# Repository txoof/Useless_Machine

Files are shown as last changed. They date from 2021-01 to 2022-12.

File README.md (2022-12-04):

# Useless Machine

## *Absolutely Useless, Completely Necessary*

UM Demo

This useless machine comes with everything you need to laser cut and assemble a box and add hardware of your choice. Both designs physically disconnect the batteries when not in use to provide months and months of useless uselessness!

It even comes in two flavors:
## [ItsyBitsy Version](ItsyBitsy_Version/ItsyBitsy_README.md)

The ItsyBitsy version is sassy, slightly passive aggressive, has lights, is programmable and hackable! It runs on AdaFruit's Circuit Python and code is well documented and easily modified with options for adding additional attack/retreat modes.

There's even a PCB schematic you can spin out from OSH Park or one of the other fab houses.
## [555 Timer Version ](555_Version/555_README.md)

This version is a fun way to explore PWM and 555 timers. The venerable 555 is a great tool for making das blinken lights, but also for driving pulse-width-modulated hardware like servos.

The 555 Version requires just a few parts and can be fabricated at home with protoboard or etching your own circuit. There are resist masks, drill instructions, a BOM and everything you need to build a your own 555 Useless Machine.

## [The Box](./enclosure/Enclosure_README.md)

Fire up the pew-pew laser and make yourself a box! Everything you need to create your own laser-cut box is here including DXF, SVG, artwork and OpenSCAD files. The DXF and SVG versions are set up for 4mm birch ply. If you intend to use something thicker or thinner, make sure you generate a new layout using the OpenSCAD files.

The OpenSCAD version is customizable takes advantage of the OpenSCAD customizer interface. M

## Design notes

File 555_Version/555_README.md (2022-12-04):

# 555 Build Instructions

This version uses the venerable 555 timer to output a pulse-width modulated signal to drive a servo to max/min positions. This is a great way to learn more about the 555 and results in a cheap mechanism to drive an extremely simple useless machine.

I built this version to learn more about 555s and wrap my head around PWM signaling. I can't say that I'm an expert in either of these things now, but this project definitely helped me grow!

Check the [enclosure readme](../enclosure/Enclosure_README.md) for details on building a laser-cut enclosure.

## Circuit

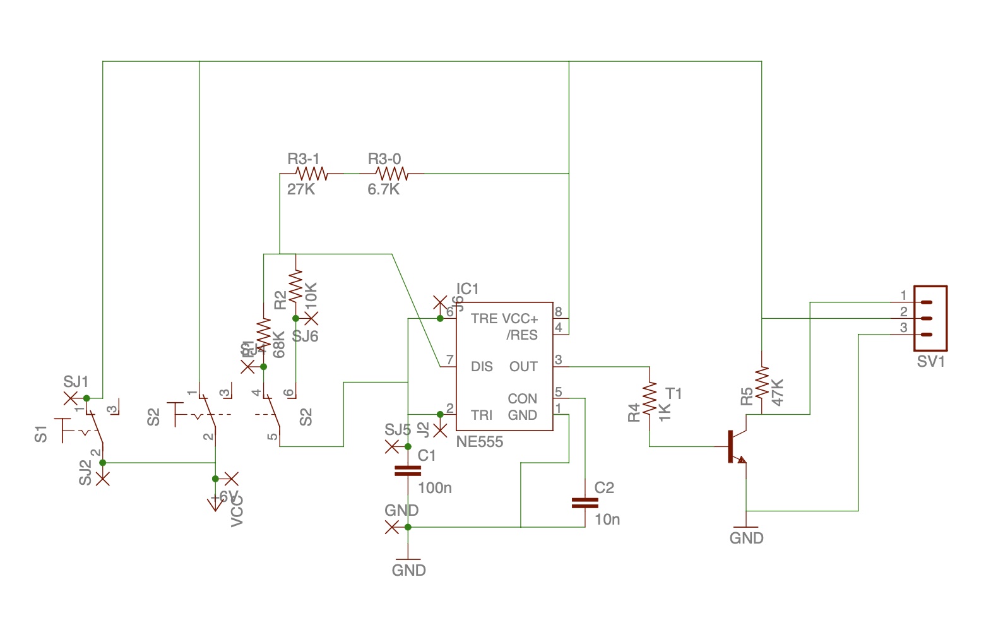
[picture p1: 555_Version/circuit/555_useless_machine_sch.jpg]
555 UM Schematic


### Bill of Materials

* S1 SPDT No/NC Roller Lever Micro Switch ([Omron SS-5GL2](https://nl.rs-online.com/web/p/micro-switches/6822660) or similar)
* S2 DPDT Panel Mount Toggle Switch ([RS PRO 734-7022](https://nl.rs-online.com/web/p/toggle-switches/7347022))
* IC1 [NE555P 8-Pin PDIP](https://nl.rs-online.com/web/p/timer-circuits/8660199)
* R1 68K
* R2 10K
* R3-1 27K
* R3-2 6.7K
* R4 1K
* R5 47K
* C1 100nF
* C2 10nF
* T1 2N2222
* [4x AA battery holder](https://nl.rs-online.com/web/p/battery-holders/1854643)
* 4x AA  battery
* 1501MG Servo or similar
* 1x3 2.54 mm Pin Headers
* hookup wire

## Circuit Board

You can build this up on prototype strip board, or use the included mask for etching your own using ferric chloride or hydrogen peroxide and muriatic acid method at home. It's pretty easy to do and some of the new toner transfer products make it pretty easy to do. Check this [instructables from TechShopJim](https://www.instructables.com/Sponge-Ferric-Chloride-Method-Etch-Circuit-Bo/) for more details.

The provided circuit board mask is for a single sided circuit and requires a couple of jumpers (see the layout). The mask is reversed and intended to go on the **bottom** of the etched board. 

* [Circuit Mask A4](./circuit/UM-Driver-rv3.1-A4.pdf)
* [Circuit Mask US Letter](./circuit/UM-Driver-rv3.1-Letter.pdf)
* [Circuit Layout w/ components](./circuit/UM-Board_Layout.pdf)

## Assembly

The Servo should run anti-clockwise when the microswitch is CLOSED and the toggle  switch is flipped toward the door.  The servo should run clockwise when the toggle switch is flipped away from the door.  

1. Etch board on a single sided copper clad pcb
2. Drill out holes:
    * Component holes are 1mm
    * Mounting holes and wire routing hole (near GND) are 3mm
3. Solder in components as shown in the board layout
4. Add a jumper wire betwen J2 and J6
5. SW1 Micro Switch is wired as Normally Open (NO)
6. SW2 DPDT switch is wired as follows:
    * SJ1 - pin 1 (same position as pin 4)  
    * SJ2 - common
    * SJ4 - pin 4 (same position as pin 1)  
    * SJ5 - common  
    * SJ6 - pin 6 
7. The signal wire of the servo is connected to pin 3 of the header; this is the pin closest to the 2N2222 transistor

## References

*hackster.io* [Controlling Servo Motor Using 555](https://www.hackster.io/techmirtz/controlling-servo-motor-using-555-dd3a33)

*EngineersGarage*: [Servo Motor Control Using a 555 Timer IC](https://www.engineersgarage.com/servo-motor-control-using-555-timer-ic/)

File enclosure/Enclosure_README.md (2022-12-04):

# Laser Cut Enclosure

Everything you need to build a laser cut enclosure is right here. The DFX and SVG versions are set up for a material thickness of ~4mm. There's even some nice artwork you can add to the outside. These instructions assume you have a working circuit and are ready to mount it in the box.

If you'd like to do some more customization or intend to use material that is not 4mm in thickness, the OpenSCAD files are designed to be hacked and modified. Check the [OpenSCAD Customization](#openscad-customization) section below for some guidance.

The lovely artwork on the outside of the box is courtesy of Patricia M. Ciuffo.

Useless Machine

## OpenSCAD Customization

If you intend to use material that is not ~4mm in thickness, you **must** adjust the material thickness variable. You can easily access this by grabbing the [OpenSCAD](./OpenSCAD/) files and libraries. Open [`useless_machine.scad`](./OpenSCAD/useless_machine.scad) and use the *Customizer* to change the `thick` (Material Thickness) value in the *Project Setup* section.

Adjusting the thickness will recalculate the finger cuts along the edges and adjust some of the other design values. Major adjustments to the thickness may impact other values. Make sure you check the 3D model for interferences and other issues.

To generate a new DXF or SVG file switch to the 2D view (*Customizer > Project Setup > 2D*). You will need to render the project (F6 or *Design > Render*) and then export the DXF or SVG (*File > Export > SVG|DXF*).

*NOTES:*

* The 3D view deliberately leaves off several of the faces. This is just to make viewing easier. They are indeed accounted for in the 2D production.
* It is possible to 3D print this enclosure, but the finger joints will likely not fit together. You will need to do some sanding of your finished parts, or change up the algorithm that calculates the inside/outside dimensions.

## Case Files

| File | Notes |
|---|---|
| [useless_machine.dxf](./useless_machine-1.34.dxf) | Case outline only compatible with lasercutting software (material thickness ~4mm) |
| [useless_machine.svg](useless_machine-1.34.svg) | Case outline as a scallable vector graphic. Use this version if you'd like to add your own vector/raster artwork (material thickness ~4mm) |
| [useless_machine.zip](./useless_machine-SCAD.zip) | Customizable OpenSCAD code for generating SVG or DXF output. Use this version if you'd like to customize the dimensions or material thickess. |
| [useless_machine_artwork.zip](./usless_machine_artwork) | Adobe Illustrator vector graphics that can be used to decorate the outside of the enclosure. |
| [OpenSCAD Files](./OpenSCAD/)| All the required files for customizing your design and generating new DXF and SVG Files|

## Assembly

| | | |
|-|-|-|
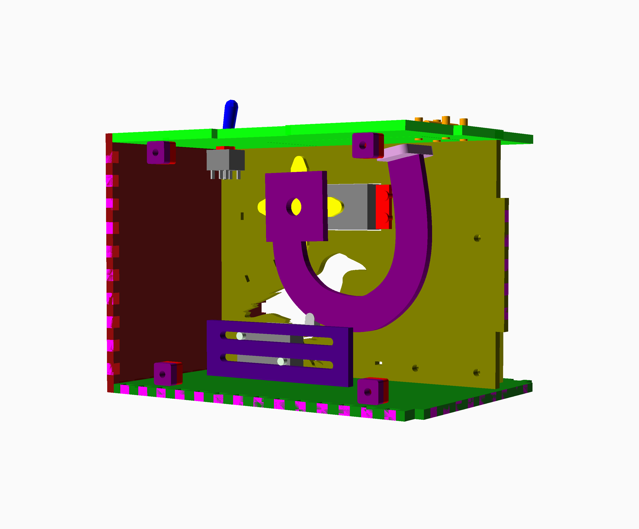
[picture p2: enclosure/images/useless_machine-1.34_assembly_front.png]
assembly front
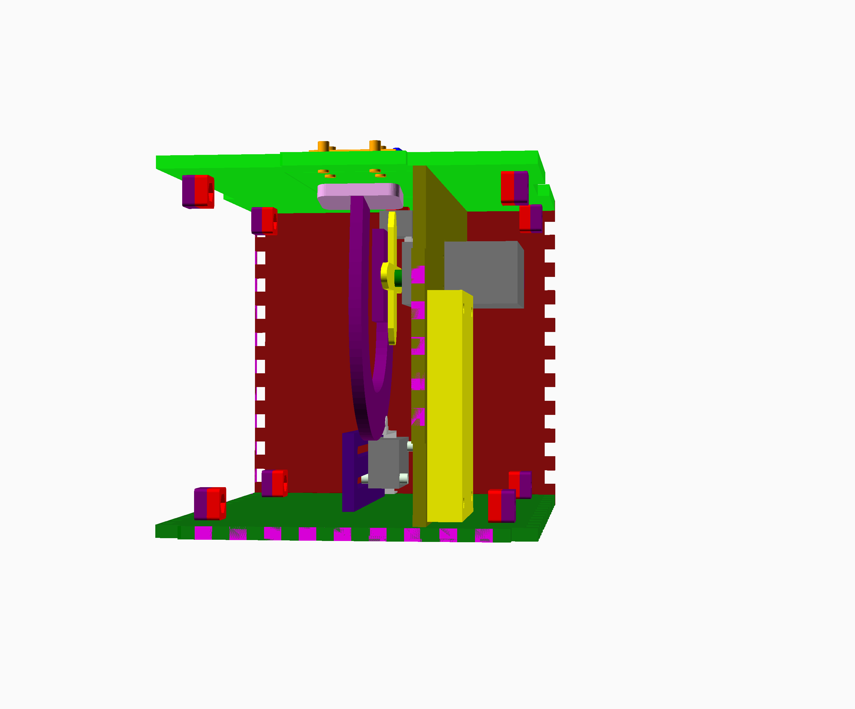
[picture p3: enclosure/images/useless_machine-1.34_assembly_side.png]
assembly side
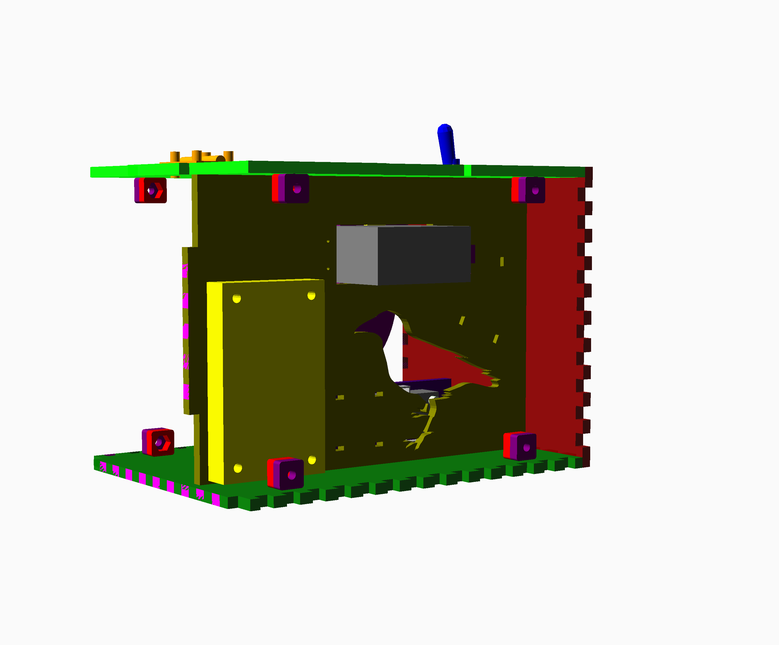
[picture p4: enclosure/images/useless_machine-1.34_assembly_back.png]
assembly back
| <br/> FRONT| | <br/> BACK|

### Materials

* 10x M3 Bolts
* 8x M3 Nuts
* 2x M2 or M3 Bolts and matching nuts
* Small hinge and bolts or screws 16mm between holes and 13mm from across faces
* PLA (wood) Glue
* Appropriate servos, switches, batteries, etc.

## Construction

The laser-cut faces should fit together logically. Use the illustrations and annotated image below to help identify the parts and orientations. 

Lay the bottom face in front of you so that the microswitch support is closest to you and oriented to the left side of the bottom plate. Slot the internal support into the bottom face. The crow should be facing to your right and should be directly in front of the microswitch support. Check the images above for reference.

Slot the microswitch support into the bottom plate. The support should be located in front of the bird cut-out.

Slot in the left and right sides. These are interchangeable unless you've decorated them.

Check the fit of the front, back and lid and then set the front, back and lid aside. Use a small amount of PLA glue to attach the supports and sides. DO NOT GLUE THE FRONT, BACK OR LID!

### Install PCB and Battery

If you are using the either of the supplied PCBs from this project, the holes should line up with the PCB Mount holes on the inside support. Use either wooden spacers or washers to raise the PCB a bit and then use M3 bolts and nuts to secure.

Depending on the mounting options for your battery pack, you can either use velcro, hot-glue or drill holes to mount it. 

Route any wires for the microswitch or DPDT switch through the bird cutout.

### Catch Construction

Build 4x LID catches using one fastener with a bolt hole, one tabbed fastener and an M3 bolt. Glue the two fastener pieces together, then glue the M3 nut into hexagonal hole. It helps to put a bolt through the nut to prevent the threads from filling with glue.
| | |
|-|-|
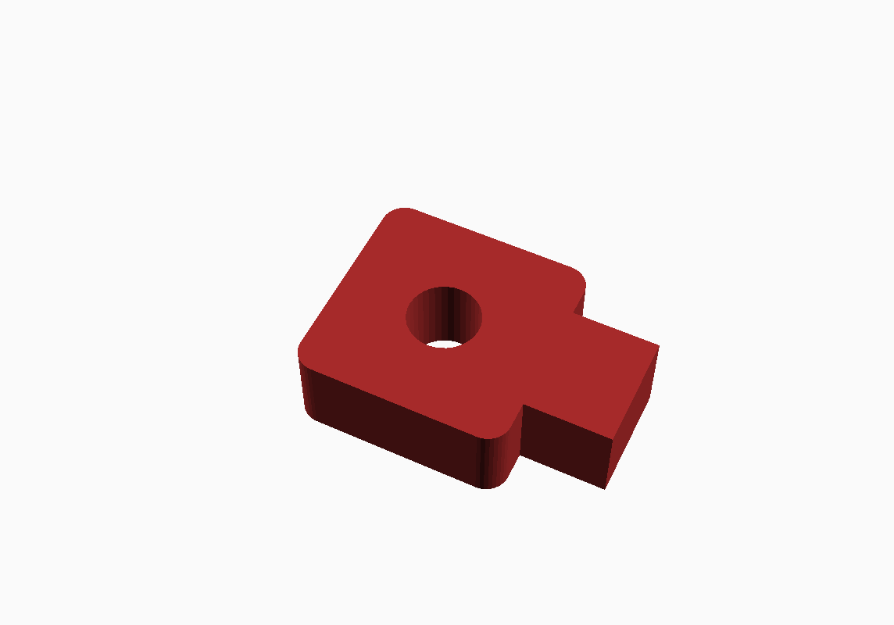
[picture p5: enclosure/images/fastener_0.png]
bolt hole fastener
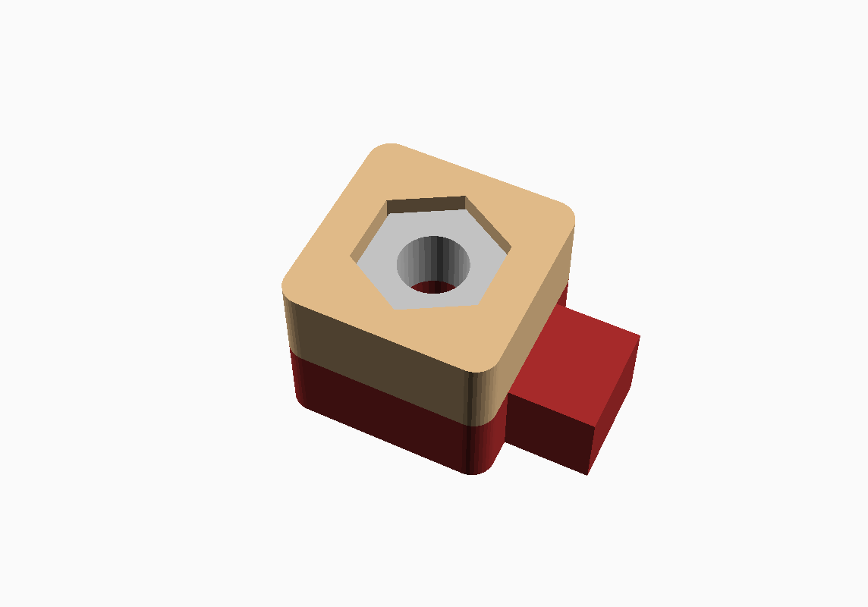
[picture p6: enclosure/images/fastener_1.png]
tabbed fastner
|| |

Build 3x BOTTOM catches using one fastener with a bolt hole, two tabbed fastener and an M3 bolt. Glue the two fastener pieces together, add an M3 nut into hexagonal hole then glue on the last tabbed fastener, but with the tab facing the opposite direction. These will be used in the fastener locations in the bottom face. Wait to glue these in until 

| | | |
|-|-|-|
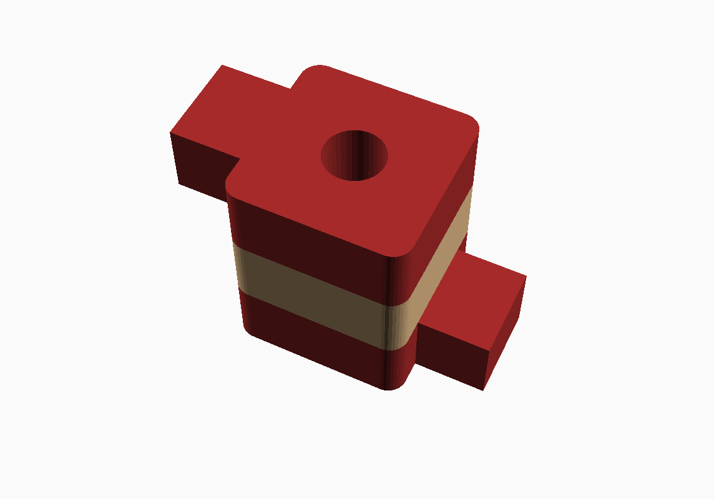
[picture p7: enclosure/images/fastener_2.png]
full stack
|bolt hole fastener|tabbed fastner ||

### Attach the Catches

UM Catches

Glue the catches into place on the lid using the method below. This method helps ensure that the catches are properly aligned with the bolt holes and the front and back faces will sit snugly.

1. Thread an M3 Bolt through the top two holes of the front and back faces
2. Loosely screw one LID catch onto the bolt so the nut is facing inwards
3. Starting with the front face, put a small dab of glue onto the two lid catches
4. Fit the face onto the base and seat all the fingers on the left and right sides
5. Orient the tabs on the LID catches so they are facing upwards
6. Place the lid on the box seating the glue-covered tabs into the fastener locations
7. Tighten the bolts so they are **finger** tight and ensure the tabs are fully seated in the lid
8. Allow the glue to dry
9. Repeat for the back face

Glue three BOTTOM catches into place on the base using the same method as the lid. Start with one side, then do the other. Depending on the thickness of your PCB, you will need to find the best possible solution for the catch directly in front of it.

### Install the Lid and Door Jamb

Using either small wood screws, or small bolts, attach the hinge to the top and the door in the lid. I added a bit of silver plastic from an anti-static bag using double stick tape to the back of the door to decrease the friction with the arm as it pushed open the door. This is optional.

If your lid does not close on its own, adding a small spring between the bolts of the hinge can help it snap back shut. A small spring out salvaged from a clicky ball-point pen worked great for this. This is optional.

To keep the lid from flopping too far inside the box, you will need to glue the door jamb to the underside of the lid. The jamb should be glued so the lip of the door opposite the hinge just rests on it.

UM door jamb

### Install the Switches

Use the raven shaped hole in the internal wall to route your wires from the PCB side of the box to the larger space opposite the PCB. 

The DPDT switch is installed in the lid through the provided hole using the nuts supplied with the switch. If your switch rotates too much, consider adding some small pieces of wood on either side (see image above).

The SPDT micro switch is installed on the Microswitch Support using two bolts and nuts. Attach the switch on the inside of the support closest to the internal wall. Loosely attach the switch for now. It will need to be adjusted after the arm is installed.

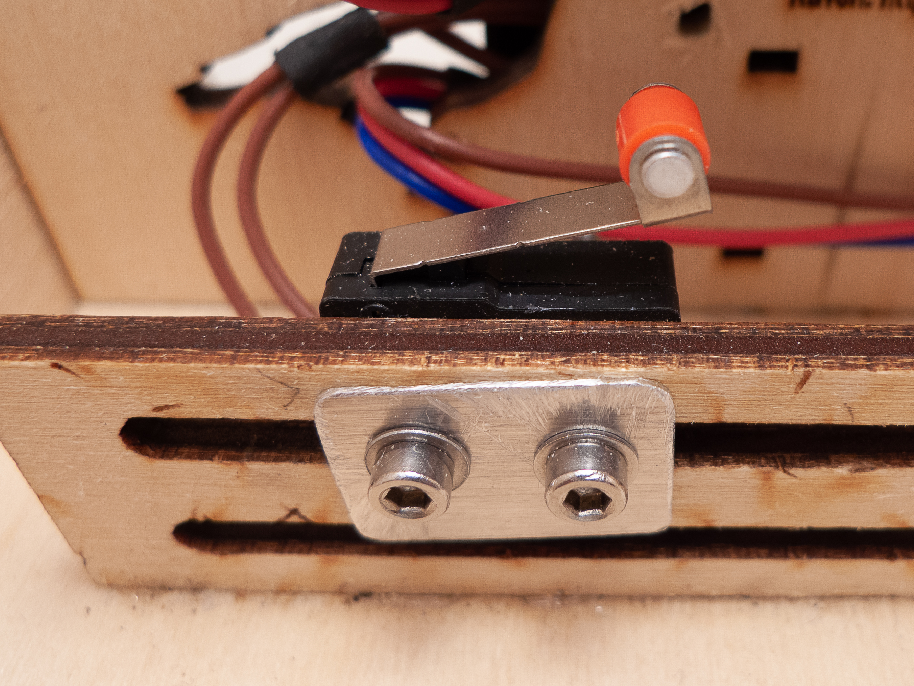
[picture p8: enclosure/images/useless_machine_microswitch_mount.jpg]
UM microswitch mount


### Install the Servo and Arm

Attach the arm to the servo horn (black or white plastic disk) supplied with the servo. Use small wood screws.  Glue the pusher face onto the arm using PLA glue.

Working from the side opposite the PCB, mount the servo so the horn (drive side) is on the same side as the microswitch. Screw the servo in place using the small wood screws supplied with the servo.

Rotate the servo clockwise until it stops. Turn it back anti-clockwise slightly less than 1/4 turn. Attach the arm and horn assembly to the servo using the screw supplied with the servo so that the arm is all the way retracted and just about touching the microswitch (see the image).

Manually rotate the arm and make sure that the pusher head can make it all the way to the switch and go just a bit further. If the arm cannot reach the switch, unmount the arm and turn the servo clockwise a few degrees. Attach the arm and try again. Repeat as needed.

UM Servo and Arm

### Adjust the Microswitch

For both the 555 and ItsyBitsy designs provided, when the arm touches the microswitch, it signals that the arm has returned *home*. For the 555 version, this disconnects the battery entirely. The ItsyBitsy version starts a countdown timer and after a preset time, disconnects a latching relay to disconnect the battery.

For both designs, the position of the limit switch is important. Limit switches come in a lot of variety with long levers, rollers and require a variety of force to switch. Slide the microswitch on the support left and right until you can find a position where the arm is completely inside the box **and** the switch is activated. 

As long as the arm isn't bottoming out and crashing into the bottom of the box, or hitting the limit of the servo, any position where the arm is entirely inside the box will work. Play with it until you find a solution you like.

### Close It Up

Tie up all your loose wires using zip ties or some twist-ties. Use the M3 bolts to close up the box and enjoy!

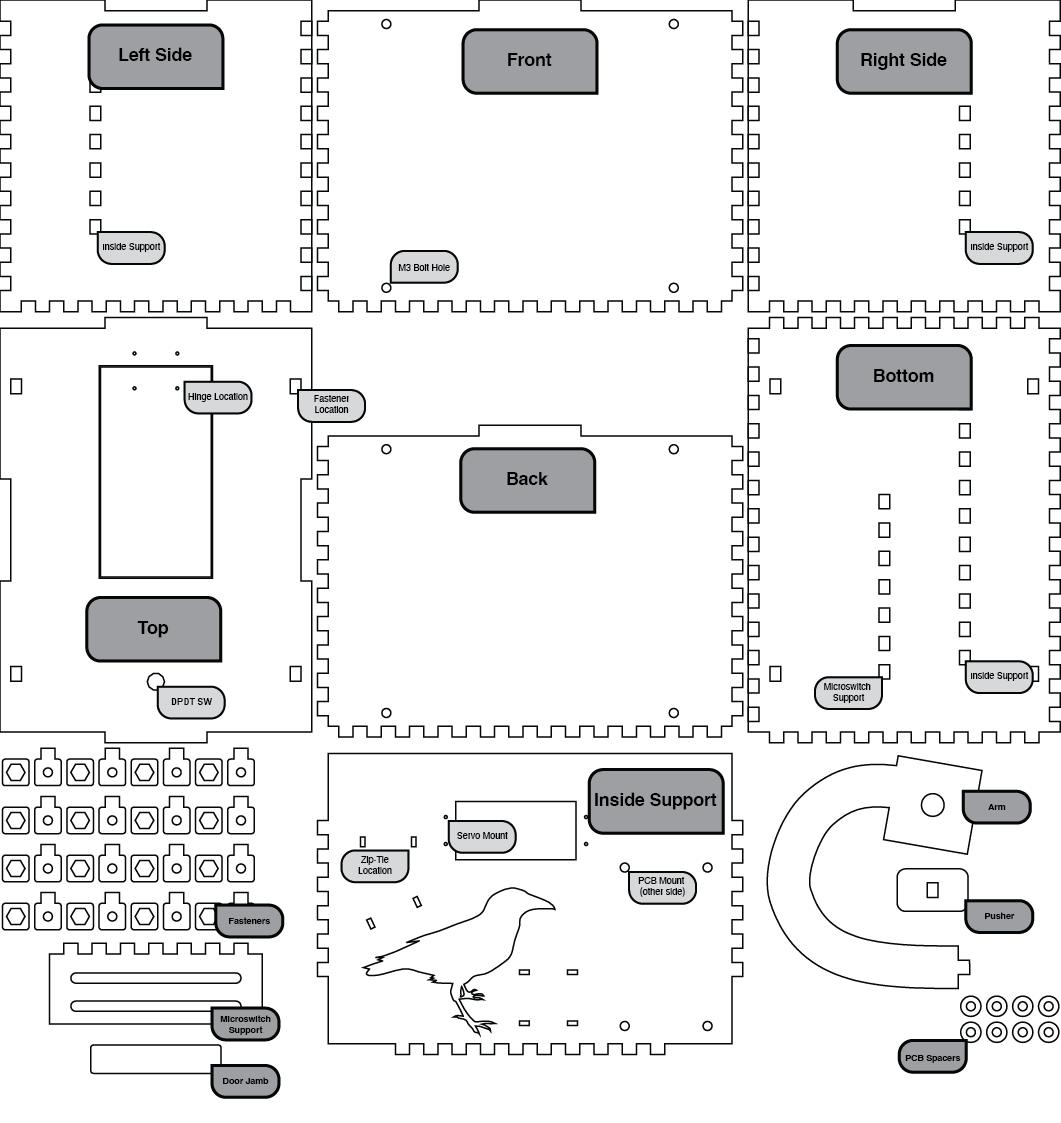
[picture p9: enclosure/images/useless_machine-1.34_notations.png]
annotated layout


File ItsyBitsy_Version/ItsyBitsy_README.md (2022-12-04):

# ItsyBitsy Useless Machine

This useless machine runs off of an AdaFruit 5V ItsyBitsy running CircuitPython. It's got sassy, random responses, neo-pixle bling and it's just as useless and **AWESOME** as all the rest.

To get the 

This design runs off of 4xAA batteries and uses a latching relay and some clever double pull double throw magic to completely disconnect the battery when it's not in use so it won't chooch through your AAs like crazy.

If you want to have your own PCB milled, you can also find the Eagle design files. I have a few extra PCBs sitting around for anyone that's interested. I'll ship them to the first lucky people that ask.

Useless Machine!

## Code

Find the code and necessary libraries in the [CircuitPython](./CircuitPython/) directory

### Pinouts

```python
# bottom limit switch (micros switch)
LIMIT_SWITCH_PHY = board.D9
# top direction switch (dpdt)
DIRECTION_SWITCH_PHY = board.D7
# servo PWM
SERVO_PWM_PHY = board.D10
# send +3v pulse to switch off relay
RELAY_OFF_PHY = board.D13
# NeoPixel driver PIN
PIXEL_PWM_PHY = board.A1
```
## Bill of Materials

[Eagle CSV version](./circuit/UM%20V2%20ItsyBitsy.csv)

|Part |Value|Device |Package |Description|ALLIED_NUMBER|DESCRIPTION |HEIGHT|MANUFACTURER_NAME|MANUFACTURER_PART_NUMBER|
|-|-|-|-|-|-|-|-|-|-|
|LED1 |LTST-C930KRKT|LTST-C930KRKT|LTSTC930KRKT|LED, Red LTST-C930KRKT, Lite-On 631 nm 3125 (1210) SMD package | |LED, Red LTST-C930KRKT, Lite-On 631 nm 3125 (1210) SMD package|2.5mm |Lite-On|LTST-C930KRKT |
|K1 |DS2E-SL2-DC5V|DS2E-SL2-DC5V|DS2ESL2DC5V |Low Signal Relays - PCB 2A 5VDC DPDT LATCHING PCB|70158678 |Low Signal Relays - PCB 2A 5VDC DPDT LATCHING PCB |10.2mm|Panasonic|DS2E-SL2-DC5V |
|C1 |470|CPOL-USE2,5-6E |E2,5-6E |POLARIZED CAPACITOR, American symbol | ||| ||
|D1 |1N4004 |1N4004 |DO41-10 |DIODE| ||| ||
|DIRECTIONSW|Direction Sw |CONN_04POLAR |MOLEX-1X4 |Multi connection point. Often used as Generic Header-pin footprint for 0.1 inch spaced/style header connections| ||| ||
|EXTPOWER |Limit Sw |CONN_02POLAR |MOLEX-1X2 |Multi connection point. Often used as Generic Header-pin footprint for 0.1 inch spaced/style header connections| ||| ||
|LIMITSW|Limit Sw |CONN_02POLAR |MOLEX-1X2 |Multi connection point. Often used as Generic Header-pin footprint for 0.1 inch spaced/style header connections| ||| ||
|NEOPIXEL |7x |CONN_03POLAR |MOLEX-1X3 |Multi connection point. Often used as Generic Header-pin footprint for 0.1 inch spaced/style header connections| ||| ||
|Q1 |2N3904 |MPS2222A-NPN-TO92-CBE|TO92-CBE|NPN Transistror| ||| ||
|R1 |100|R-US_M1206 |M1206 |RESISTOR, American symbol| ||| ||
|R2 |220|R-US_M1206 |M1206 |RESISTOR, American symbol| ||| ||
|SERVO|1051 M |CONN_03POLAR |MOLEX-1X3 |Multi connection point. Often used as Generic Header-pin footprint for 0.1 inch spaced/style header connections| ||| ||
|U$1|ITSYBITSY3V|ITSYBITSY3V|ITSYBITSY3V |AdaFruit ItsyBitsy M4 3V | ||| ||

## Eagle Files

Find the eagle files in the [circuit](./circuit/) folder.

I've had lots of success working with [OSH Park](https://oshpark.com/). Their instructions are incredibly clear and the service is great.

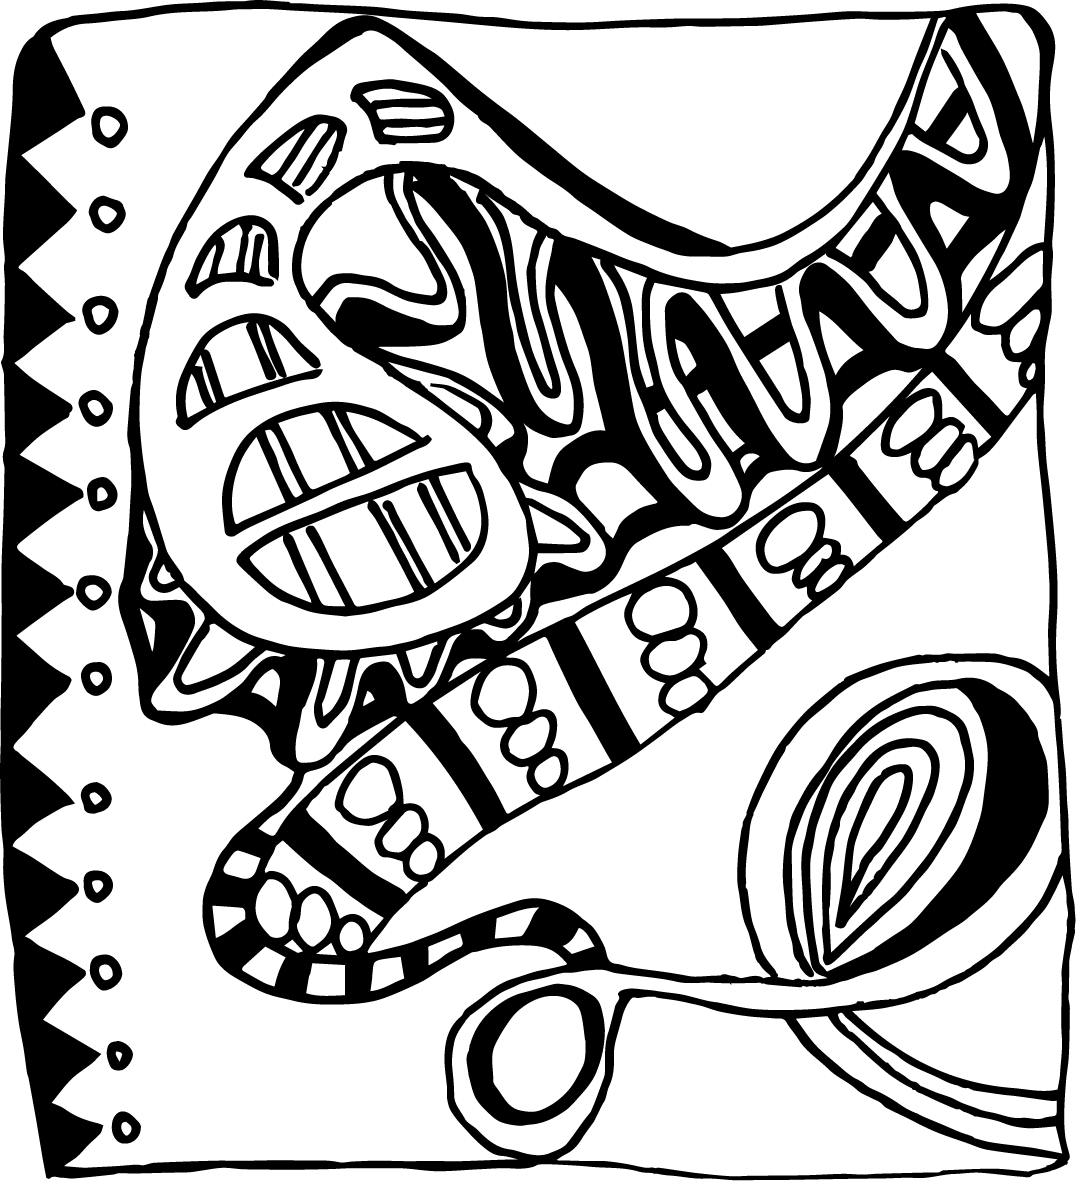
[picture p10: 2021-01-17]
enclosure/usless_machine_artwork/FaceA_Arches.tif

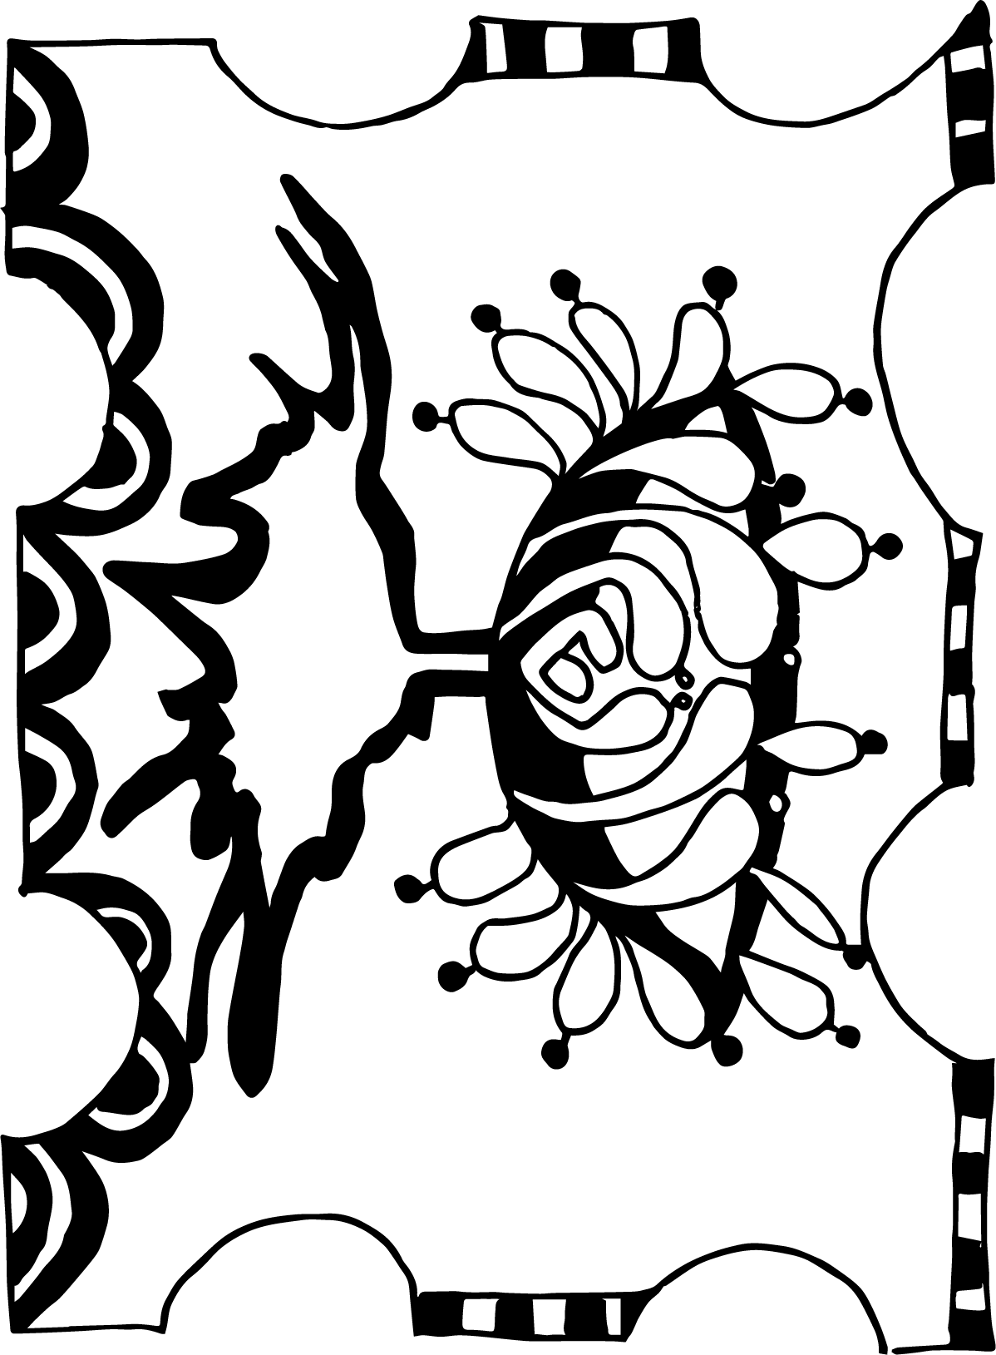
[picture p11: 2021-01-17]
enclosure/usless_machine_artwork/FaceBC_Cup.tif

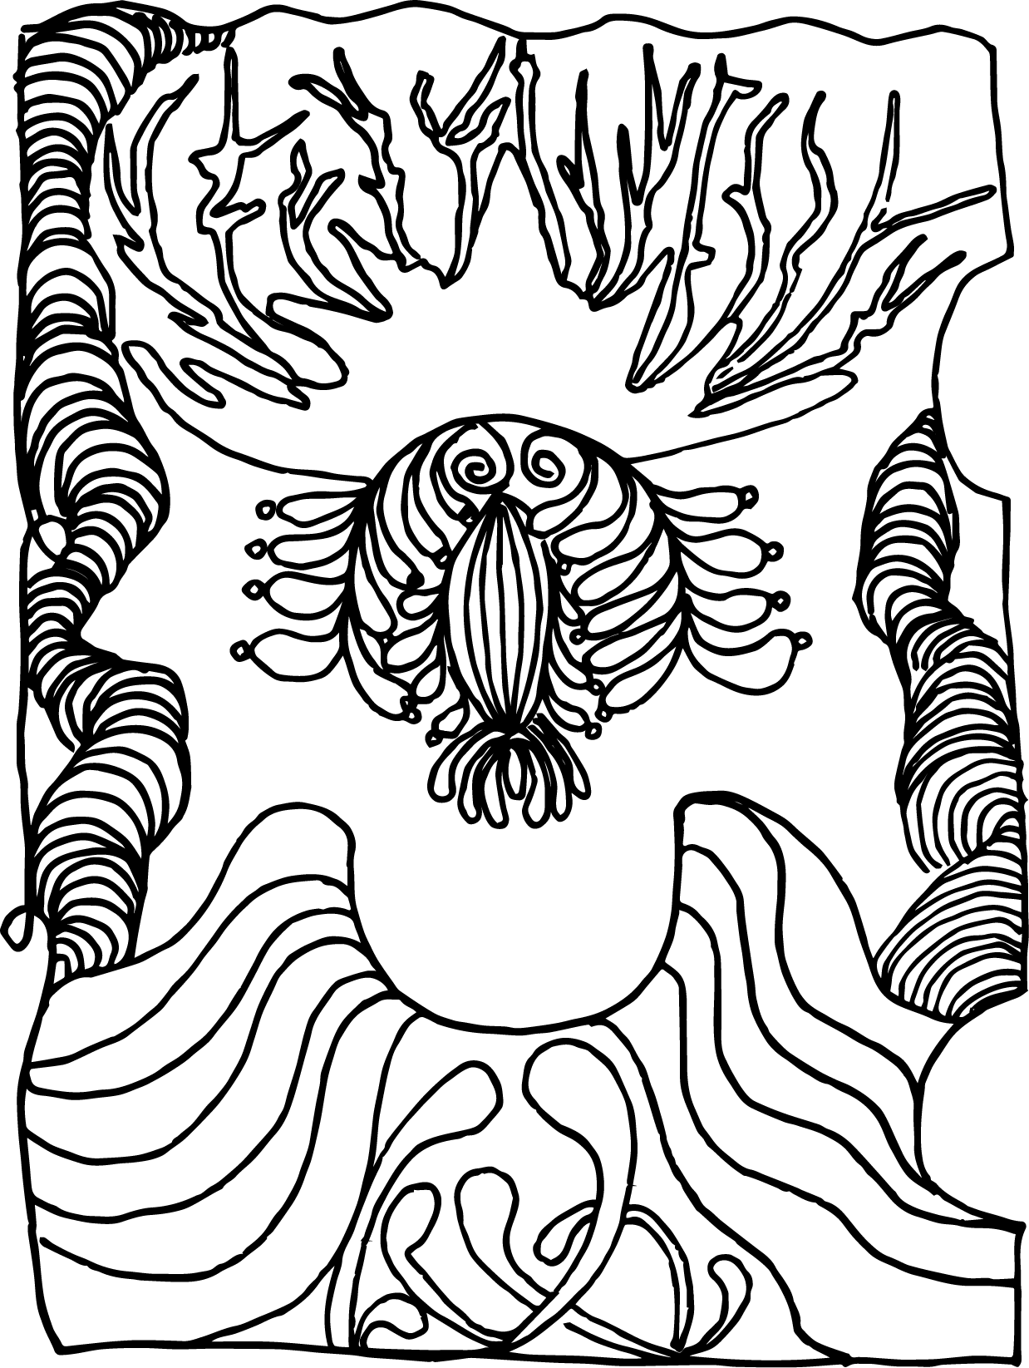
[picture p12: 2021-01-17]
enclosure/usless_machine_artwork/FaceBC_Flower Vertical_lid.tif

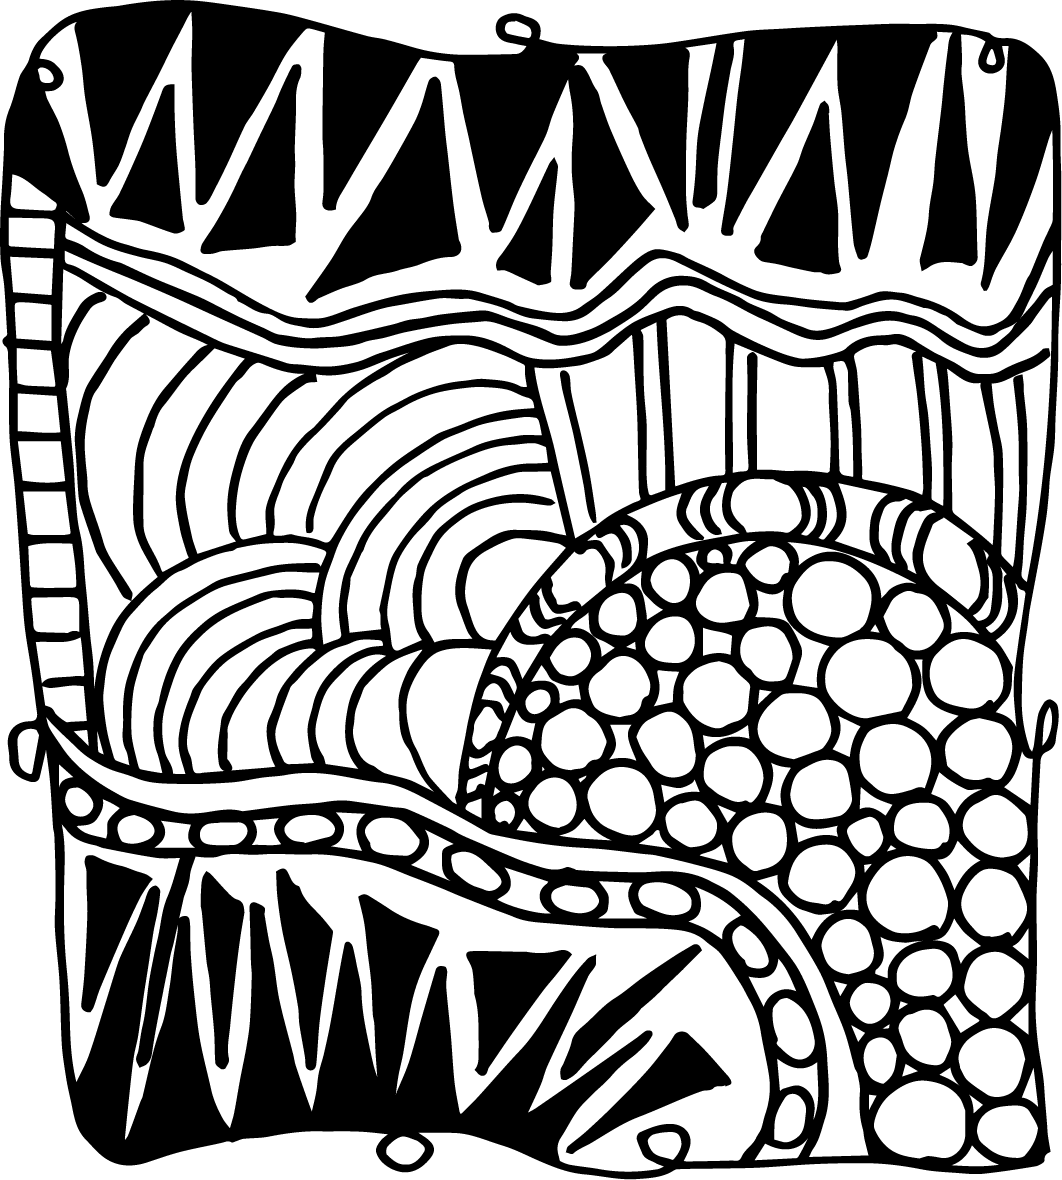
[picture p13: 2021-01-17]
enclosure/usless_machine_artwork/FaceA_Bubbles.tif

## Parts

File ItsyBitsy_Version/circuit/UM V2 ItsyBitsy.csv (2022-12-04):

Part | Value | Device | Package | Description | ALLIED_NUMBER | DESCRIPTION | HEIGHT | MANUFACTURER_NAME | MANUFACTURER_PART_NUMBER | MOUSER_PART_NUMBER | MOUSER_PRICE-STOCK | POPULARITY | PROD_ID | RS_PART_NUMBER | RS_PRICE-STOCK | SF_ID | SPICEPREFIX
C1 | 470 | CPOL-USE2,5-6E | E2,5-6E | POLARIZED CAPACITOR, American symbol |  |  |  |  |  |  |  |  |  |  |  |  | C
D1 | 1N4004 | 1N4004 | DO41-10 | DIODE |  |  |  |  |  |  |  | 82
DIRECTIONSW | Direction Sw | CONN_04POLAR | MOLEX-1X4 | Multi connection point. Often used as Generic Header-pin footprint for 0.1 inch spaced/style header connections |  |  |  |  |  |  |  |  | CONN-08186 |  |  | PRT-08231
EXTPOWER | Limit Sw | CONN_02POLAR | MOLEX-1X2 | Multi connection point. Often used as Generic Header-pin footprint for 0.1 inch spaced/style header connections |  |  |  |  |  |  |  |  |  |  |  | PRT-09918
K1 | DS2E-SL2-DC5V | DS2E-SL2-DC5V | DS2ESL2DC5V | Low Signal Relays - PCB 2A 5VDC DPDT LATCHING PCB | 70158678 | Low Signal Relays - PCB 2A 5VDC DPDT LATCHING PCB | 10.2mm | Panasonic | DS2E-SL2-DC5V
LED1 | LTST-C930KRKT | LTST-C930KRKT | LTSTC930KRKT | LED, Red LTST-C930KRKT, Lite-On 631 nm 3125 (1210) SMD package |  | LED, Red LTST-C930KRKT, Lite-On 631 nm 3125 (1210) SMD package | 2.5mm | Lite-On | LTST-C930KRKT | 859-LTST-C930KRKT | https://www.mouser.com/Search/Refine.aspx?Keyword=859-LTST-C930KRKT |  |  | 1689768 | http://uk.rs-online.com/web/p/products/1689768
LIMITSW | Limit Sw | CONN_02POLAR | MOLEX-1X2 | Multi connection point. Often used as Generic Header-pin footprint for 0.1 inch spaced/style header connections |  |  |  |  |  |  |  |  |  |  |  | PRT-09918
NEOPIXEL | 7x | CONN_03POLAR | MOLEX-1X3 | Multi connection point. Often used as Generic Header-pin footprint for 0.1 inch spaced/style header connections |  |  |  |  |  |  |  |  | CONN-08625 |  |  | PRT-08096
Q1 | 2N3904 | MPS2222A-NPN-TO92-CBE | TO92-CBE | NPN Transistror |  |  |  |  |  |  |  | 0
R1 | 100 | R-US_M1206 | M1206 | RESISTOR, American symbol |  |  |  |  |  |  |  |  |  |  |  |  | R
R2 | 220 | R-US_M1206 | M1206 | RESISTOR, American symbol |  |  |  |  |  |  |  |  |  |  |  |  | R
SERVO | 1051 M | CONN_03POLAR | MOLEX-1X3 | Multi connection point. Often used as Generic Header-pin footprint for 0.1 inch spaced/style header connections |  |  |  |  |  |  |  |  | CONN-08625 |  |  | PRT-08096
U$1 | ITSYBITSY3V | ITSYBITSY3V | ITSYBITSY3V | AdaFruit ItsyBitsy M4 3V

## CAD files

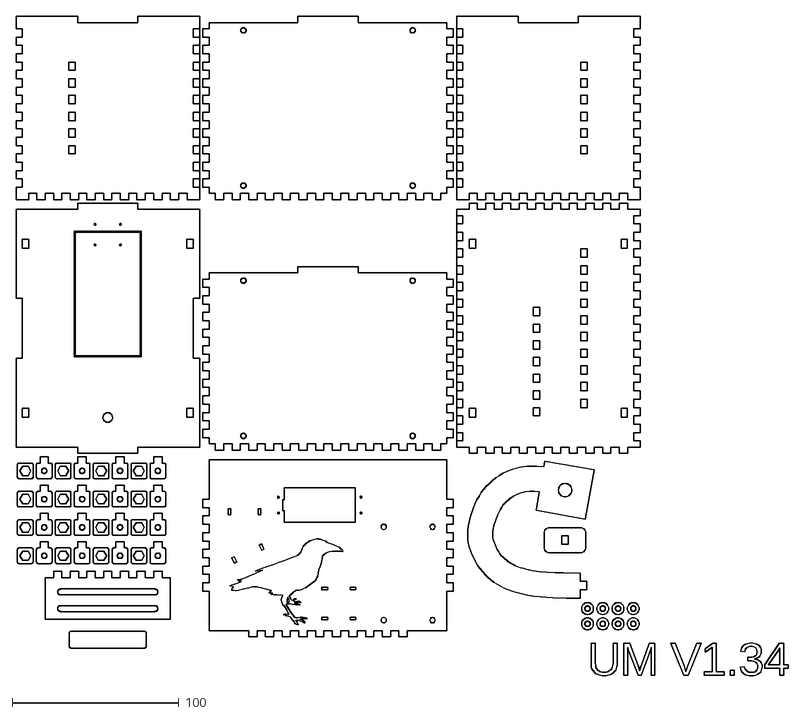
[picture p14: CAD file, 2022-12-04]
enclosure/useless_machine-1.34.dxf
462.7 x 395.3

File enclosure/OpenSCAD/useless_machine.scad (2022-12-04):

/*
Useless Machine! By Aaron Ciuffo 
*/


//servo
//use <./libraries/futabaS3004.scad>
use <./libraries/hitec-HS422.scad>
//toggle switch
use <./libraries/toggle_switch.scad>
//mockup of external hinge
use <./libraries/stardard_hinge.scad>
//lever actuated micro switch
use <./libraries/micro_switch-variant.scad>
use <./libraries/micro_switch.scad>
//rough mockup of a 4XAA 6V battery pack
use <./libraries/4AA_battery.scad>

/*[Project Setup]*/
VERSION="UM V1.34";
// Layout 2D or 3D
2D=0; //[1:2D for DXF, 0:3D for Preview]
//Material Thickness
thick=3.8;
//separation of finished pieces in 2D layout
separation=2;
//transparency of 3D model
alpha=5; //[1:100]


/*[Box Outside Dimensions]*/
//Box Width - X
bX=110;
//Box Depth - Y
bY=150;
//Box Height - Z
bZ=110; //100 -testing adjustments for microswtich
//arm material thickness
armThick=thick;

/*[Box Features]*/
//Include a lid?
addLid=1; //[1:Lid, 0:No Lid]
//Finger Hole Diameter - 0==no hole
//holeDia=0; //[0:50] -- moved into switch configuration
holeFacets=36;//[3:36]
//lid fastners
lidCatch=1; //[0:no catch, 1:catch]
cornerR=1; //corner radius on lid catch
lidBolt=3; //metric bolt size for sizing nut

/*[Finger Width]*/
//Finger width (NB! width must be < 1/3 shortest side)
fingerW=5;//[3:20]
//Lid finger width 
fingerLidW=36;//[3:20]




/*[Internal Support]*/
//horn to bottom of flange 17.6, armThickness=thickness of arm material
supXpos=-thick/2-17.6-armThick/2;

/*[Servo Position]*/
//placement on internal support
serX=0; // just off center to accomodate arm thickness
serY=-15; //-10 
serZ=79;   

/*[Switch]*/
switchX=0;
switchY=-53.5; //48.5
swtichZ=0;
switchDia=6.05;
holeDia=switchDia;

/*[Arm]*/
//size of hole
armHX=40; //35
armHY=75; //50
//border to remove around hole opening to allow smooth open/close
armHBorder=thick/4;
//position of hole from edge
armFromYEdge=17;
// files for arm
armFile="./libraries/arm_rv1.dxf";
headFile="./libraries/pusher_head_rv1.dxf";
armRot=11; //off position
armRotAnim=$t*110; // rotate to +105 to see switch fliping position
//Door jamb dimensions
doorJX=armHX+6;
doorJY=10;


/*[Hinge Dimensions]*/
//hingeX=15.3;
//hingeY=18.2;
//Larger Hinge
hingeX=18.8;
hingeY=25.6;


/*[Internal Supports]*/
//bDimension/Ratio to determines the length and number of tabs on internal supports
//switch support
ssRatio=2;
//internal support Z dimension ratio to decrease the tabs by
isRatioZ=1.5;
//internal support Y dimension ratio to decrease the tabs by
isRatioY=1.3;



/*[Battery Pack]*/
//dimensions - useful for calculations below
batX=58.5; 
batY=64;
batZ=16;
batPosX=30;
batPosY=35;
batPosZ=0;

/*[Driver Board]*/
//Driver Board dimensions
brdX=66;
brdY=40;
brdZ=10;
brdFile="./libraries/driver_board_rv1.dxf";
//position
brdXpos=0;
brdYpos=48;
brdZpos=-17;
//mounting bolt diameter (m size)
brdBlt=3;

/*[Micro Switch]*/
//Dimensions of switch 
mswX=20;
mswY=10.3;
mswZ=14;
mswXpos=0;
mswYpos=-29;
//FIXME consider adjusting this if the microswitch does not fit properly
mswZpos=8.5; // was 8

//position for the switch support
swXsup=0;
swYsup=-20;
swZaup=0;

/*[Wire Routing Hole]*/
holeY=-bY/6;
holeZ=-bZ/5;
holeScale=1.5;
holeFile="./libraries/raven_rv1.dxf";

/*[Zip Tie Holes]*/
zTieX=3.5; //width
zTieZ=1.6; //thickness
zTieY=18; //distance betwen holes
// Locations for zip ties [X, Y, Z, rotation]
zTieLoc=[
          [-48, -5, 0, -65],
          [-50, 20, 0, 90],
          [-2, -35, 0, 0], 
          [15, -35, 0 , 0] ];


/*[Hidden]*/
//transparency alpha
alp=1-alpha/100;

//Catch Dimensions
f=1.8*lidBolt; //flat distance is 1.8 * m bolt diameter
r=(f*1/cos(30))/2; //radius of metric nut
catch=r*3-2*cornerR; //catch X and Y dimensions


//cuts that fall complete inside the edge
module insideCuts(length, fWidth, cutD, uDiv) {
  //Calculate the number of fingers and cuts
  numFinger=floor(uDiv/2);
  numCuts=ceil(uDiv/2);

  //draw out rectangles for slots
  for (i=[0:numCuts-1]) {
    translate([i*(fWidth*2), 0, 0])
      square([fWidth, cutD]);
  }
}

//cuts that fall at the end of an edge requirng an extra long cut
module outsideCuts(length, fWidth, cutD, uDiv) {
  numFinger=ceil(uDiv/2);
  numCuts=floor(uDiv/2);
  //calculate the length of the extra long cut
  endCut=(length-uDiv*fWidth)/2;
  //amount of padding to add to the itterative placement of cuts 
  // this is the extra long cut at the beginning and end of the edge
  padding=endCut+fWidth;
  
  square([endCut, cutD]);

  for (i=[0:numCuts]) {
    if (i < numCuts) {
      translate([i*(fWidth*2)+padding, 0, 0])
        square([fWidth, cutD]);
    } else {
      translate([i*(fWidth*2)+padding, 0, 0])
        square([endCut, cutD]);
    }
  }
}

module lidCatch(boltHole=true, project=false, tab=false, pct=1.05) {
  if (project==false) {
    //center on the base of the tab to make positioning easier
    translate([0, -catch/2-cornerR])
    difference() {
      union() {
        hull() {
          square(catch, center=true);
          //iterate over quadrants I-IV 
          //place a circle in each corner to make the rounded square hull
          for (i=[ [-1, 1], [1, 1], [1, -1], [-1, -1]]) {
            translate([i[0]*(catch/2), i[1]*(catch/2)])
              circle(r=cornerR, $fn=36);
          } // close for
        } //close hull

        //add a tab to the piece without the nut hole
        if (boltHole==false) {
          translate([0, (catch/2+cornerR)+thick/2])
            square([fingerW, thick], center=true);
        } //close if bolthole
      } //close union
      if (boltHole==true) {
        circle(r=r*pct, $fn=6);
      } else {
        circle(r=lidBolt/2*pct, $fn=36);
      } // close if boltHole
    } //close difference
  } else { //close if project 
    if (tab==false) {
      translate([0, -catch/2-cornerR])
        circle(r=lidBolt/2*pct, $fn=36);
    } else {
        //center the tab projection
        square([fingerW*pct, thick], center=true);
    } 
  }
}

module boardStandOff(r=2, c=4) {
  inRad=brdBlt/2*1.05;
  outRad=inRad+2;
  for (i = [0:r-1] ) {
    translate([0, -i*(outRad*2+separation), 0])
    for (j = [0:c-1]) { 
      translate([j*(outRad*2+separation), 0])
        difference() {
          circle(r=outRad, $fn=36);
          circle(r=inRad, $fn=36);
        }
    }
  }
  
}


//Punch holes in the other faces to match the tabs on the support
module supportPunch(length, fWidth, cutD, uDiv) {
  //subract 4 tabs to make the support less intrusive.
  //TODO find a better way of dealing with this; breaks down below 30mm with 5mm tabs
  locuDiv=uDiv-4;
  numFinger=ceil(locuDiv/2);
  numCuts=floor(locuDiv/2);

  //calculate the length of the extra long cut
  endCut=(length-uDiv*fWidth)/2;
  //amount of padding to add to the itterative placement of cuts 
  // this is the extra long cut at the beginning and end of the edge
  padding=endCut+fWidth;
  
//  square([endCut, cutD]);
  
  for (i=[0:numCuts]) {
    translate([i*(fWidth*2)+endCut, -cutD/2, 0])
      square([fWidth, cutD]);

  }
}


//Punch holes in other faces to match the tabs on an internal support
module holePunch(length, uDiv, Q=2) {
  divLoc = (floor(uDiv/Q)%2)==0 ? floor(uDiv/Q)-1 : floor(uDiv/Q);
  numCuts=floor(divLoc/2);
  
  locLength=bY/Q; //length of support = boxY/Q
  endCut=(locLength-divLoc*fingerW)/2;
  translate([-divLoc*fingerW/2-endCut, 0, 0])
  for (i=[0:numCuts]) {
    translate([i*(fingerW*2)+endCut, -thick/2, 0])
      square([fingerW, thick]);
  }
}

module armHole() {
  difference() {
    square([armHX, armHY], center=true);
    square([armHX-armHBorder, armHY-armHBorder], center=true);
  }
}

module zipTie() {
  translate([0, -zTieY/2, 0])
    square([zTieX, zTieZ], center=true);
  translate([0, zTieY/2, 0])
    square([zTieX, zTieZ], center=true);

}

//Face A (X and Z dimensions)
//Front and back face
module faceA(uDivX, uDivY, uDivZ, uDivLX, uDivLY) {
  difference() {
    square([bX, bZ], center=true);

    //X+/- edge (X axis in OpenSCAD)
    //if true, make cuts for the lid, otherwise leave a blank edge
    if (addLid) {
      translate([-uDivLX*fingerLidW/2, bZ/2-thick, 0])
        insideCuts(length=bX, fWidth=fingerLidW, cutD=thick, uDiv=uDivLX);
    }
    translate([-uDivX*fingerW/2, -bZ/2, 0]) 
      insideCuts(length=bX, fWidth=fingerW, cutD=thick, uDiv=uDivX);

    //Z+/- edge (Y axis in OpenSCAD)
    translate([bX/2-thick, uDivZ*fingerW/2, 0]) rotate([0, 0, -90])
      insideCuts(length=bZ, fWidth=fingerW, cutD=thick, uDiv=uDivZ);
    translate([-bX/2, uDivZ*fingerW/2, 0]) rotate([0, 0, -90])
      insideCuts(length=bZ, fWidth=fingerW, cutD=thick, uDiv=uDivZ);

    translate([supXpos, 0, 0]) rotate([0, 0, -90])
      //supportPunch(length=bZ, fWidth=fingerW, cutD=thick, uDiv=uDivZ); 
      holePunch(length=bZ, uDiv=uDivZ, Q=isRatioZ);
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

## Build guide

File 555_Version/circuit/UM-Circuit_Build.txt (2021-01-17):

Build Instructions

01) Etch board on a single sided copper clad pcb
02) Component holes are 1mm
03) Mounting holes and wire routing hole (near GND) are 3mm
04) Solder in components as shown in the board layout
05) Add a jumper wire betwen J2 and J6
06) DPDT switch should be connected as follows:
    SJ1 - pin 1 (same position as pin 4)  
    SJ2 - common   
    SJ4 - pin 4 (same position as pin 1)  
    SJ5 - common  
    SJ6 - pin 6  
    
    The Servo should run anti-clockwise when the microswitch is CLOSED and the toggle
    switch is flipped toward the door.  The servo should run clockwise when the toggle
    switch is flipped away from the door.  

07) Snap Switch/Micro Switch should be connected as NO 
08) The signal wire (white on Futaba servos) should be connected to pin 3 of the header;
    this is the pin closest to the 2N2222 transistor

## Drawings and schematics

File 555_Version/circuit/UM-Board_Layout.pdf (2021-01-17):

S2

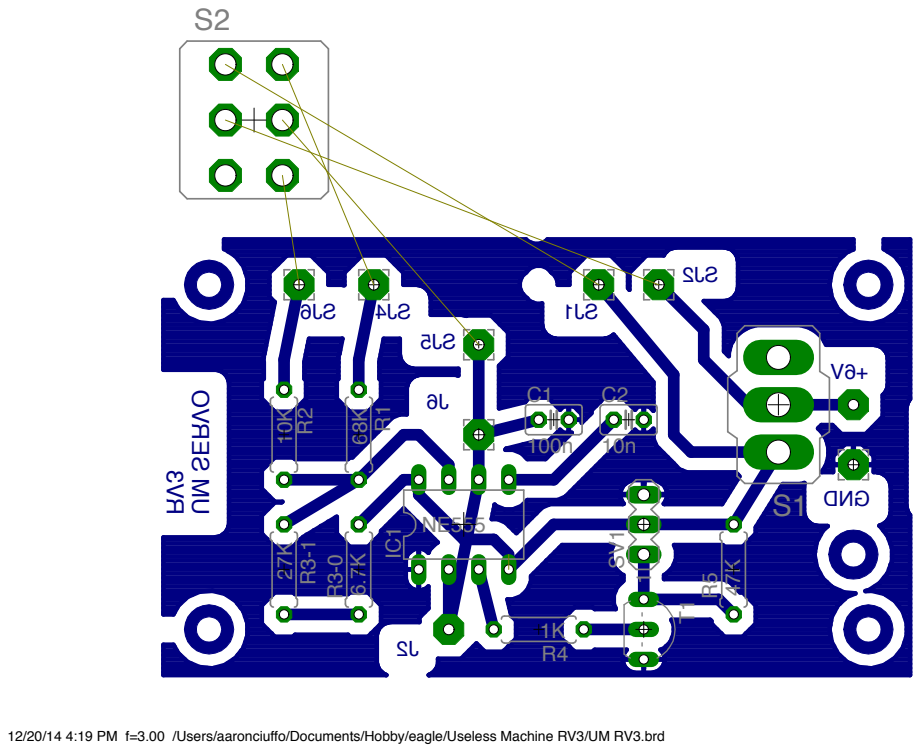
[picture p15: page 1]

12/20/14 4:19 PM f=3.00 /Users/aaronciuffo/Documents/Hobby/eagle/Useless Machine RV3/UM RV3.brd RV³ UM SERVO

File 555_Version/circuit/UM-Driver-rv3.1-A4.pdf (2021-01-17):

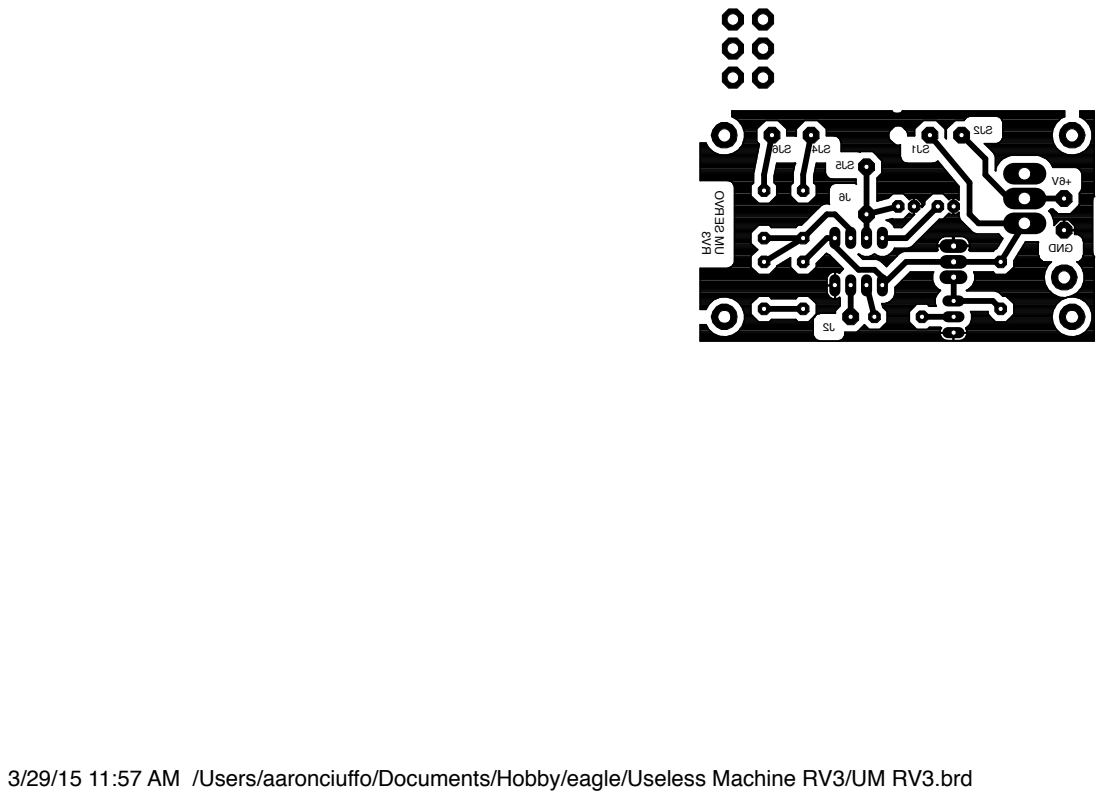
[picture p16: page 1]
GND

3/29/15 11:57 AM /Users/aaronciuffo/Documents/Hobby/eagle/Useless Machine RV3/UM RV3.brd RV³ UM SERVO

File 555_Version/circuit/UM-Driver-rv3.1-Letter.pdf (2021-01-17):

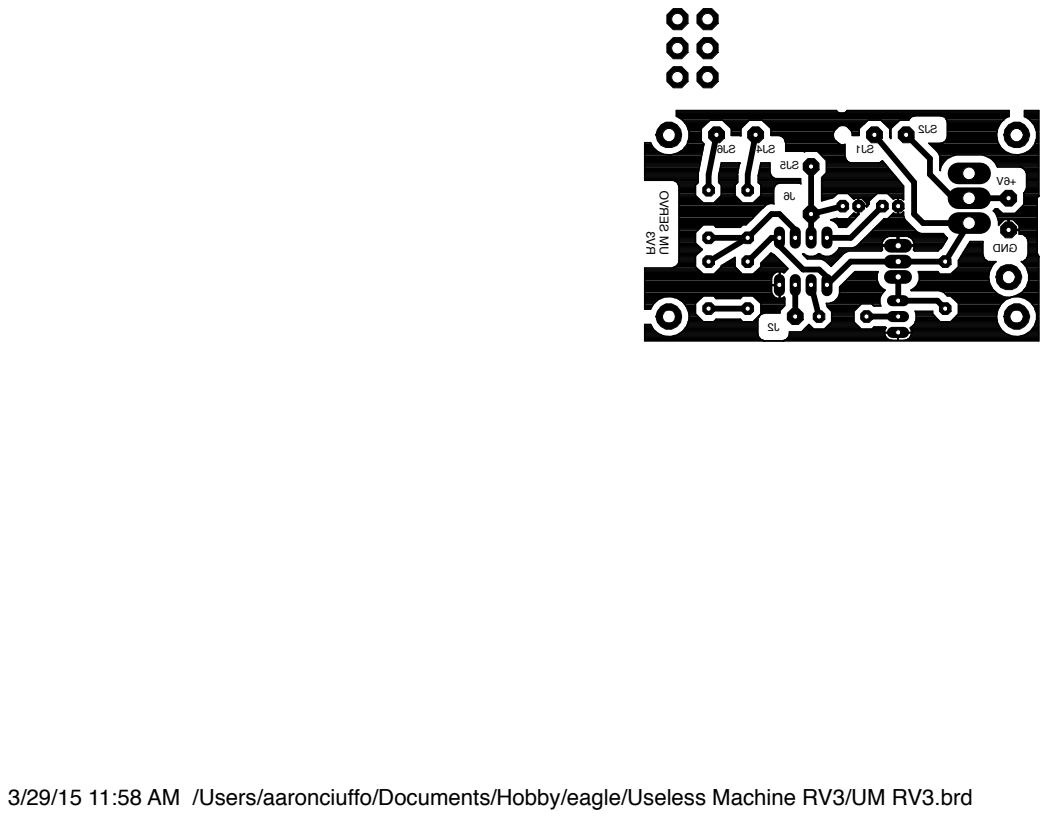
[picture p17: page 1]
GND

3/29/15 11:58 AM /Users/aaronciuffo/Documents/Hobby/eagle/Useless Machine RV3/UM RV3.brd RV³ UM SERVO

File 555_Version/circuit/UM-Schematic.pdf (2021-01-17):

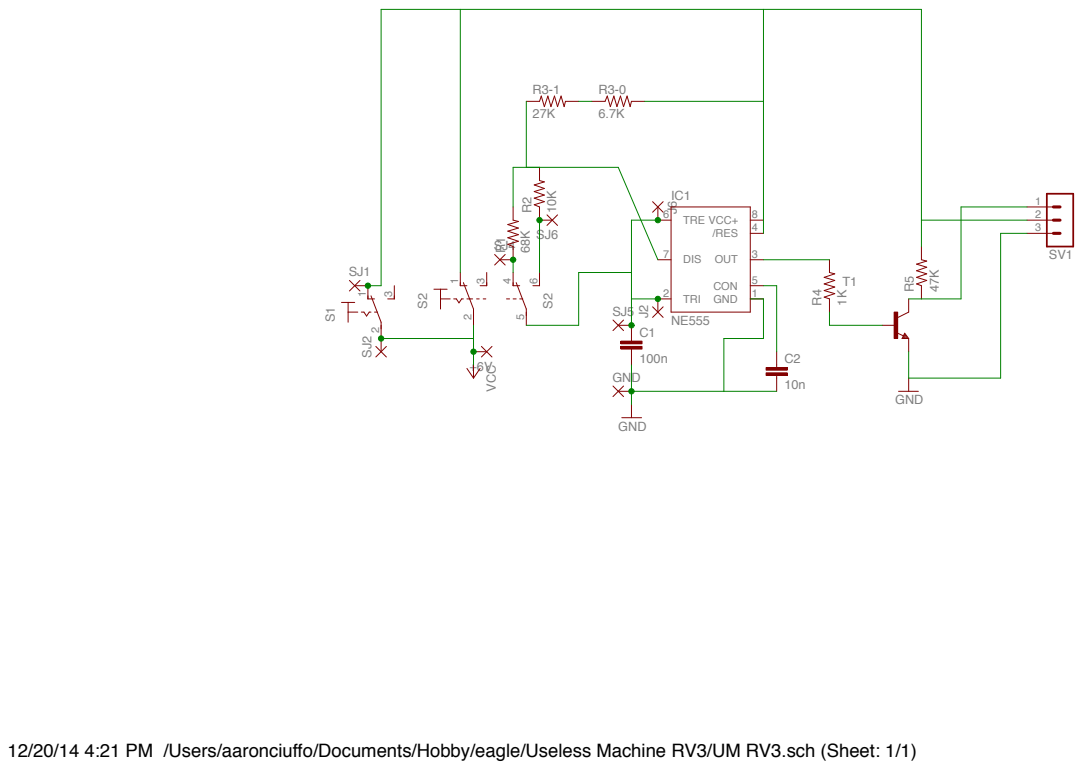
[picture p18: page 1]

12/20/14 4:21 PM /Users/aaronciuffo/Documents/Hobby/eagle/Useless Machine RV3/UM RV3.sch (Sheet: 1/1)

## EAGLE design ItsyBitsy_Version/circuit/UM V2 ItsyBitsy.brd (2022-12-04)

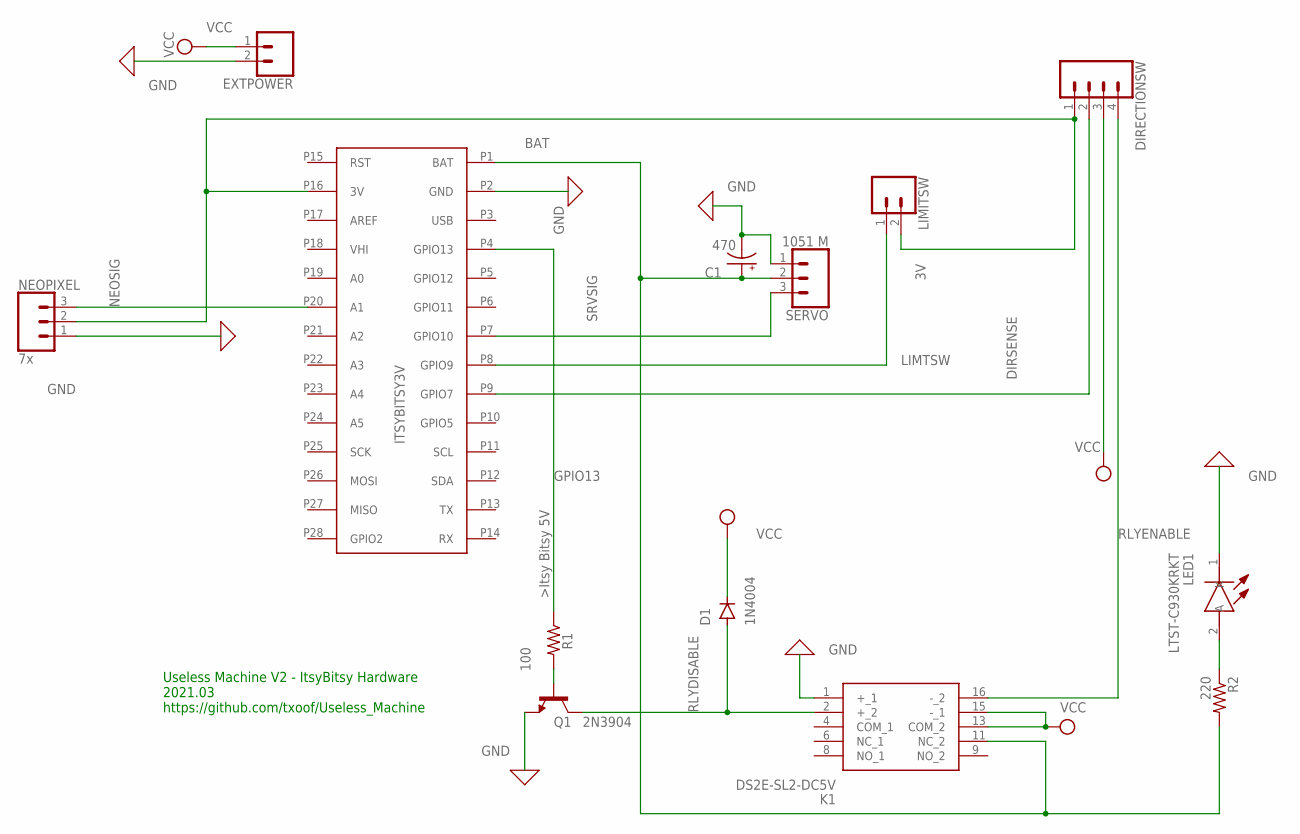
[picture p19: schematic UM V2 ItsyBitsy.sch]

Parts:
C1: 470; E2,5-6E
D1: 1N4004; DO41-10
DIRECTIONSW: Direction Sw; MOLEX-1X4
EXTPOWER: Limit Sw; MOLEX-1X2
K1: DS2E-SL2-DC5V; DS2ESL2DC5V
LED1: LTST-C930KRKT; LTSTC930KRKT
LIMITSW: Limit Sw; MOLEX-1X2
NEOPIXEL: 7x; MOLEX-1X3
Q1: 2N3904; TO92-CBE
R1: 100; M1206
R2: 220; M1206
SERVO: 1051 M; MOLEX-1X3
U$1: ITSYBITSY3V

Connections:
3V: DIRECTIONSW.1, LIMITSW.2, NEOPIXEL.2, U$1.P16 (3V)
BAT: C1.+, K1.11 (NC_2), R2.2, SERVO.2, U$1.P1 (BAT)
DIRSENSE: DIRECTIONSW.2, U$1.P9 (GPIO7)
GND: C1.-, EXTPOWER.2, K1.1 (+_1), LED1.1 (K), NEOPIXEL.1, Q1.E, SERVO.1, U$1.P2 (GND)
GPIO13: R1.1, U$1.P4 (GPIO13)
LIMTSW: LIMITSW.1, U$1.P8 (GPIO9)
unnamed: LED1.2 (A), R2.1
unnamed: Q1.B, R1.2
NEOSIG: NEOPIXEL.3, U$1.P20 (A1)
RLYDISABLE: D1.A, K1.2 (+_2), Q1.C
RLYENABLE: DIRECTIONSW.4, K1.16 (-_2)
SRVSIG: SERVO.3, U$1.P7 (GPIO10)
VCC: D1.C, DIRECTIONSW.3, EXTPOWER.1, K1.13 (COM_2), K1.15 (-_1)

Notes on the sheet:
Useless Machine V2 - ItsyBitsy Hardware 2021.03 https://github.com/txoof/Useless_Machine

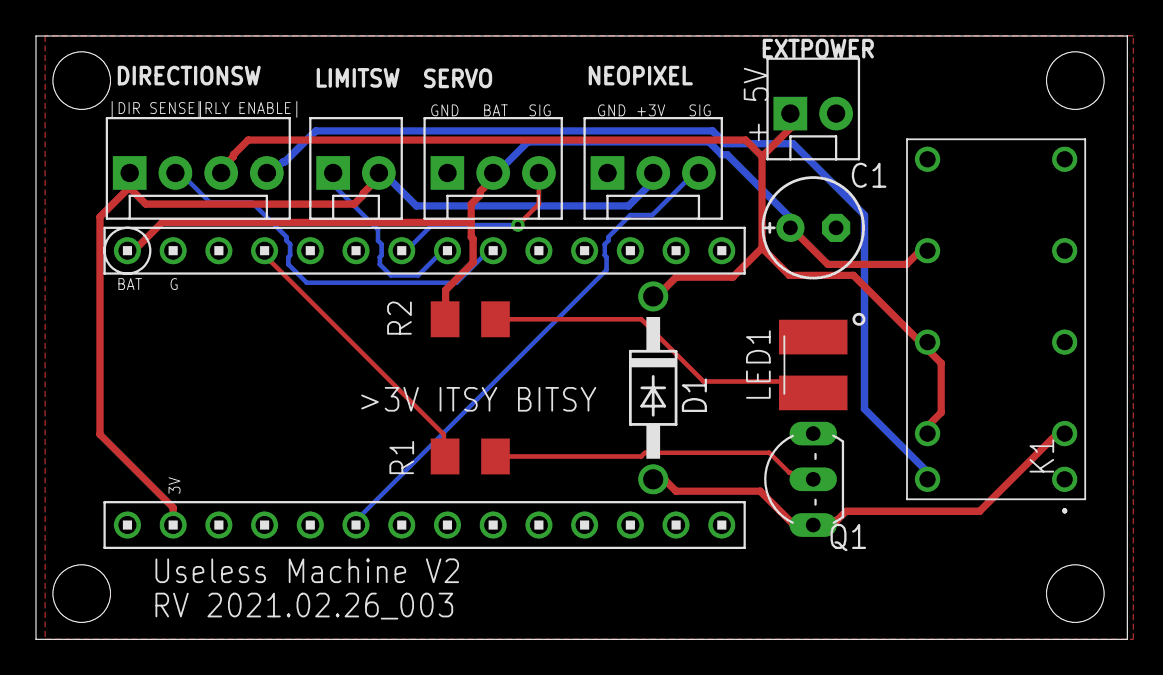
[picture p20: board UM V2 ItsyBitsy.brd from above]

Board: 2 copper layers, 60.6 x 33.5 mm, 13 parts (0 on the bottom side), 13 nets.

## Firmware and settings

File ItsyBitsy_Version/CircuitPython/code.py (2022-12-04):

import board
import digitalio
import time
# import pulseio
import pwmio
import neopixel
from os import urandom
import random




from adafruit_debouncer import Debouncer


##### CONSTANTS  #####
# shutoff timeout (seconds)
SHUTDOWN_TIMEOUT = 10

# endstop positions for arm - determine these through trial and error
HOME_LOW = 43
HOME_HIGH = 168.5

# bottom limit switch for detecting when the arm is "home"
LIMIT_SWITCH_PHY = board.D9

# top direction switch DPDT switch
DIRECTION_SWITCH_PHY = board.D7

# servo PWM
SERVO_PWM_PHY = board.D10

# The latching relay is latched on by the DPDT switch
# After the program has sat idle, send +3v pulse to switch off relay and disconnect battery
RELAY_OFF_PHY = board.D13

# NeoPixel driver PIN
PIXEL_PWM_PHY = board.A1
NUM_PIX = 7
PIX_BRIGHT_MAX = 1
PIX_BRIGHT_MIN = 0.01
RED = (255, 0, 0)
RED_LT = (240,128,128)
ORANGE = (255, 128, 0)
ORANGE_LT = (255,69,0)
PINK = (255, 20, 147)
YELLOW = (255, 150, 0)
GREEN = (0, 255, 0)
GREEN_DK = (85,107,47)
CYAN = (0, 255, 255)
BLUE = (0, 0, 255)
NAVY = (0, 0, 128)
PURPLE = (180, 0, 255)
BLACK = (0, 0, 0)


# min and max duty cycle for PWM servo 0.5==0 degrees; 2.5==180 degrees
DUTY_MIN = 0.5 # 0 degrees
DUTY_MAX = 2.5 # 180 degrees

# min and max step size for rotating servo (degrees)
RESOLUTION_MIN = 0.04 # smallest angle steps to take when moving
RESOLUTION_MAX = 6 # largest angle steps to take when moving

# max, min angle
ANGLE_MIN = 0
ANGLE_MAX = 180

# soft landing program step for parking arm - this should always be the last
# step for a retreat program
SOFT_LANDING = (None, None, 0.25)

##### /CONSTANTS #####

def heart_beat(t=10):
    # simply outputs a tick to the console; helpful in debugging
    global timer

    if time.monotonic() - timer >= t:
        timer = time.monotonic()
        print(f'tick: {timer}')
        return True
    else:
        return False



##### PIN OBJECTS  #####
limit_switch_pin = digitalio.DigitalInOut(LIMIT_SWITCH_PHY)
limit_switch_pin.direction = digitalio.Direction.INPUT
limit_switch_pin.pull = digitalio.Pull.DOWN
# Debounce the lmit switch - this is critical
limit_switch = Debouncer(limit_switch_pin)

direction_switch_pin = digitalio.DigitalInOut(DIRECTION_SWITCH_PHY)
direction_switch_pin.direction = digitalio.Direction.INPUT
direction_switch_pin.pull = digitalio.Pull.DOWN
# debounce the DPDT direction switch on the outside of the box
direction_switch = Debouncer(direction_switch_pin)

# relay power-off pin 
relay_pin = digitalio.DigitalInOut(RELAY_OFF_PHY)
relay_pin.direction = digitalio.Direction.OUTPUT

# servo pwm OUTPUT
servo = pwmio.PWMOut(SERVO_PWM_PHY, duty_cycle=2**15, frequency=50)


# NeoPixel pwm OUTPUT
pixels = neopixel.NeoPixel(PIXEL_PWM_PHY, NUM_PIX, brightness=PIX_BRIGHT_MAX,
                           auto_write=False)
##### /PIN OBJECTS #####

def map_range(a, b, s):
    '''Map range (min a, max a) to range (min b, max b) for value s
    '''
    (a1, a2), (b1, b2) = a, b
    return b1 + ((s - a1) * (b2 - b1) / (a2 - a1))

def angle_to_duty(angle, frequency=50):
    '''convert angle between ANGLE_MIN-ANGLE_MAX to a position between DUTY_MIN-DUTY_MAX'''
    pulse_ms = map_range((ANGLE_MIN, ANGLE_MAX), (DUTY_MIN, DUTY_MAX), angle)

    period_ms = 1.0 / frequency * 1000.0
    return int(pulse_ms / (period_ms / 65535.0))

def go_to_angle(dest_angle):
    '''move servo directly to angle'''
    print(f'moving to: {dest_angle}')
    servo.duty_cycle = angle_to_duty(dest_angle)

def rotate_to_angle(current_angle, dest_angle, attack, speed=0.08):
    '''rotate from current_angle to dest_angle at speed
    Args:
        current_angle (real): angle between SERVO_MIN and SERVO_MAX
        dest_angle (real): angle between SERVO_MIN and SERVO_MAX
        attack (bool): True - arm moves out (ccw), False - arm moves in (cw)
        speed (real): between 0 and 1
    '''
    def check_angle(angle):
        '''check if angle is out of range'''
        if angle > HOME_HIGH:
            angle = HOME_HIGH
        if angle < HOME_LOW:
            angle = HOME_LOW
        return angle

    # set the direction multiplier (positive is attack, negative retreat)
    direction = 1 if current_angle < dest_angle else -1

    break_out = False

    breakout_msg = None

    step_size = map_range((0, 1), (RESOLUTION_MIN, RESOLUTION_MAX), speed)
    steps = int(abs((current_angle-dest_angle)/step_size))

    print(f'ROTATE to {dest_angle}; speed: {speed}')

    for i in range(0, steps+1):
        limit_switch.update()
        direction_switch.update()
        # print(f'direction: {direction}\nattack: {attack}\ndirection_switch: {direction_switch.value}\n')

        if direction == 1 and attack == True and direction_switch.value == True:
            break_out = True
            breakout_msg = 'direction switch changed to "True" '

        if direction == -1 and attack == False and direction_switch.value == False:
            break_out = True
            breakout_msg = 'direction switch changed to "False"'

        if direction == -1 and limit_switch.value == True:
            break_out = True
            breakout_msg = 'bottom limit siwtch hit'


        if break_out:
            print(f'{breakout_msg}')
            break

        else:
            current_angle = current_angle + (step_size * direction)

            # if over-run in positive or negative, set to max or min as appropriate
            current_angle = check_angle(current_angle)
            servo.duty_cycle = angle_to_duty(current_angle)

    current_angle = check_angle(current_angle)
    print('')
    return current_angle, break_out

def pause(s):
    '''pause for s seconds using monotonic timer (non blocking)
    change in direction_switch will break out of pause

    Args:
        s(real): seconds to pause

    Returns:
        bool: true if pause was interrupted by a switch state change
    '''
    t = time.monotonic()
    limit_switch.update()
    direction_switch.update()

    direction_switch_current = direction_switch.value
    break_out = False
    breakout_msg = None

    print(f'pausing for {s} seconds')
    while time.monotonic() - t < s:
        limit_switch.update()
        direction_switch.update()

        if direction_switch.value != direction_switch_current:
            breakout_msg = 'user changed switch, pause canceled'
            break_out = True

        if break_out:
            print(breakout_msg)
            break

    return break_out

def find_index(current_angle, program, attack=True):
    '''find the first tuple who's 0th element is closest to current_angle

    Args:
        current_angle(real): angle of arm
        program(list of tuple): attack/retreat program
        attack(bool): true - search for first element that is >= current_angle
                      false - search for first element that is <= current_angle
    '''

    # for attack
    for i, val in enumerate(program):
        try:
            if attack:
                if val[0] >= current_angle:
                    break
            else:
                if val[0] <= current_angle:
                    break
        except TypeError:
            next

    return i



##### GLOBALS  #####
# Attack/Retreat routines
# Format: [(angle, speed, pause, color), ()]
# angle(real: 0-180),
# speed(real: 0.01-1),
# sec. pause(real)
# color(3-tuple of int)
## TODO:  move to external file


# coy
att_peek_a_boo = [(62, .3, None, PINK), (None, None, 1, PINK),
              (HOME_LOW+2, .7, None, CYAN), (None, None, .5, CYAN),
              (70, .3, None, PINK), (None, None, 1, PINK),
              (HOME_LOW+2, .7, None, CYAN), (None, None, .5, CYAN),
              (HOME_HIGH-10, .6, None, ORANGE),
              (HOME_HIGH, .1, None, ORANGE)]

# standard in and out
att_standard = [(90, .8, None, RED),
                   (110, .7, None, RED),
                   (HOME_HIGH - 15, .7, None, RED),
                   (HOME_HIGH, .1, None, RED)]

#hurry up and wait
att_hurry_wait = [(90, .9, None, GREEN),
                  (130, .9, None, GREEN),
                  (150, .9, None, GREEN),
                  (None, None, 4, GREEN_DK),
                  (HOME_HIGH, .1, None, GREEN)]


att_ever_slower = [(90, .3, None, RED),
                   (110, .2, None, RED_LT),
                   (130, .1, None, ORANGE_LT),
                   (145, .05, None, ORANGE),
                   (150, .02, None, PINK),
                   (HOME_HIGH, .01, None, PINK)]

att_array = [att_standard, att_peek_a_boo, att_hurry_wait, att_ever_slower]
att_dict = {'A.Standard': att_standard,
            'A.Peek A Boo': att_peek_a_boo,
            'A.Hurry Up and Wait': att_hurry_wait,
            'A.Ever Slower': att_ever_slower}


ret_standard = [(150, .6, None, BLUE),
                (70, .6, None, BLUE),
                (60, .4, None, BLUE),
                (50, .2, None, BLUE),
                (HOME_LOW, .05, None, BLUE),
                (None, None, .25)]

ret_ever_slower = [(150, .3, None, RED),
                   (145, .2, None, RED_LT),
                   (130, .1, None, ORANGE_LT),
                   (80, .05, None, ORANGE),
                   (50, .02, None, PINK),
                   # (HOME_LOW - 5, .01, None, PINK),
                   (HOME_LOW, .01, None, BLUE),
                   (None, None, .25)]

                   # (90, .3, None, RED),
                   # (110, .2, None, RED_LT),
                   # (130, .1, None, ORANGE_LT),
                   # (145, .05, None, ORANGE),
                   # (150, .02, None, PINK),
                   # (HOME_HIGH, .01, None, PINK)]

ret_just_checking = [(150, .5, None, BLUE),
                     (None, None, 1, NAVY),
                     (120, .5, None, BLUE),
                     (None, None, 1, NAVY),
                     (50, .8, None, BLUE),
                     (None, None, .5, NAVY),
                     (62, .3, None, RED),
                     (None, None, 1.25, NAVY),
                     (50, .1, None, BLUE),
                     (None, None, .5, NAVY),
                     (62, .3, None, RED),
                     (None, None, 1.25, NAVY),
                     (50, .1, None, BLUE),
                     (None, None, .5),
                     (100, .6, None, PINK),
                     (None, None, 1.25, NAVY),
                     (50, .4, None, BLUE),
                     (HOME_LOW, 0.05, None, BLUE)]

ret_aggressive = [(150, .9, None, NAVY),
               (70, .9, None, NAVY),
               (50, .6, None, NAVY),
               (HOME_LOW, 0.05, None, NAVY),
               (None, None, 0.25)] # all retreat programs need this at the end to ensure it stops



ret_array = [ret_standard, ret_aggressive, ret_just_checking, ret_ever_slower]
ret_dict = {'R.Standard': ret_standard,
            'R.Aggressive': ret_aggressive,
            'R.Just Checking, Don\'t Trust Ya': ret_just_checking,
            'R.Ever Slower': ret_ever_slower}

# Set default programs
att_default = 'A.Standard'
ret_default = 'R.Standard'

# set these equal to a particular program to override random choice
# set to `None` for random choice
att_test = None
ret_test = None

# last state of limit switch
limit_switch_last = None
# last state of direction switch
direction_switch_last = None

# global timer
timer = time.monotonic()

# shutdown timer
shutdown_timer = time.monotonic()
# shutdown state
is_shutdown = False
# arm is parked
is_parked = True
# timeout time expired
is_timedout = False

first_run = True

attack = None

# set initial angle
current_angle = HOME_LOW + 1

color = BLACK
seed = int.from_bytes(urandom(4), 'big')
##### /GLOBALS #####

# make sure the arm is parked to start
go_to_angle(current_angle)
time.sleep(.1)


while True:
    if heart_beat(1.5):
        if not is_shutdown:
            print(f'time to shutdown: {time.monotonic() - shutdown_timer - SHUTDOWN_TIMEOUT}')
        if is_shutdown:
            print('idle: relay off')
    limit_switch.update()
    direction_switch.update()

    is_parked = True if limit_switch.value and direction_switch.value else False
    is_timedout = True if time.monotonic() - shutdown_timer >= SHUTDOWN_TIMEOUT else False

    if is_parked == False:
        # reset the shutdown timer
        # shutdown_timer = time.monotonic()
        # reset the timout and shutdown bools
        is_timedout = False
        is_shutdown = False
    else:
        pixels.fill(BLACK)
        pixels.show()

    if is_parked and is_timedout and not is_shutdown:
        print('sending shutdown pulse')
        relay_pin.value = True
        time.sleep(1)
        relay_pin.value = False
        is_shutdown = True

    if direction_switch.value == False:
        seed = int.from_bytes(urandom(4), 'big')
        msg = '**********ATTACK!**********'
        attack = True

        # always run standard program on first run
        if first_run:
            print(f'first run after boot using default program: {att_default}')
            program = att_dict[att_default]
        else:
            # program = random.choice(att_array)
            program_name = random.choice(list(att_dict.keys()))
            print(f'PROGRAM: {program_name}')
            program = att_dict[program_name]


        # override with test attack
        if att_test:
            print('using test attack program')
            program = att_test
    elif direction_switch.value == True and limit_switch.value == False:
        seed = int.from_bytes(urandom(4), 'big')
        msg = '**********RETREAT!**********'
        attack = False

        if not program[-1] == SOFT_LANDING:
            program.append(SOFT_LANDING)
        # always run standard program on boot
        if first_run:
            print(f'first run after boot using default program: {ret_default}')
            program = ret_dict[ret_default]
            # set first_run to False
            first_run = False
        else:
            program_name = random.choice(list(ret_dict.keys()))
            print(f'PROGRAM: {program_name}')
            program = ret_dict[program_name]


        # override with test retreat
        if ret_test:
            print('using test attack program')
            program = ret_test
    else:
        msg = 'none'
        attack = None

    if attack is not None:
        print(msg)

        program_index = find_index(current_angle=current_angle,
                        program=program, attack=attack)
        program_slice = program[program_index:]

        for i in program_slice:
            # reset shutdown_timer while loop is running
            # shutdown_timer = time.monotonic()

            try:
                color = i[3]
            except IndexError:
                color = BLACK
            print(f'color: {color}')
            pixels.fill(color)
            pixels.write()
            # check if this program step is a pause step
            if i[2]:
                break_out = pause(i[2])
            else:
                current_angle, break_out = rotate_to_angle(current_angle=current_angle,
                                           dest_angle=i[0],
                                           attack=attack,
                                           speed=i[1])

            if break_out:
                print('breaking out of attack/retreat program')
                # reset the shutdown timer to start counting down after
                # program is executed
                shutdown_timer = time.monotonic()
                break

    if limit_switch.value != limit_switch_last:
        print(f'limit switch state: {limit_switch.value}')
        limit_switch_last = limit_switch.value
    if direction_switch.value != direction_switch_last:
        print(f'direction switch state: {direction_switch.value}')
        direction_switch_last = direction_switch.value

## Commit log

2021-01-17 initial circuitpython commit
2022-12-04 Reorganization of repo and addition of readmes
    [UM RV3.1.sch, UM V2 ItsyBitsy.brd, UM V2 ItsyBitsy.csv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]

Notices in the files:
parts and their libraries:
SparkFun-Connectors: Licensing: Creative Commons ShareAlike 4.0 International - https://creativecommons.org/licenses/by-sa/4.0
